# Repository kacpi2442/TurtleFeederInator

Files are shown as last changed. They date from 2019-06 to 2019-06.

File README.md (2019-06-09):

# TurtleFeederInator

Automatic turtle/fish feeder that you can 3D print yourself.
It uses WeMos D1 mini (ESP8266) as main board and features food run out sensor.

It can be powered either from USB or DC Jack (5V).

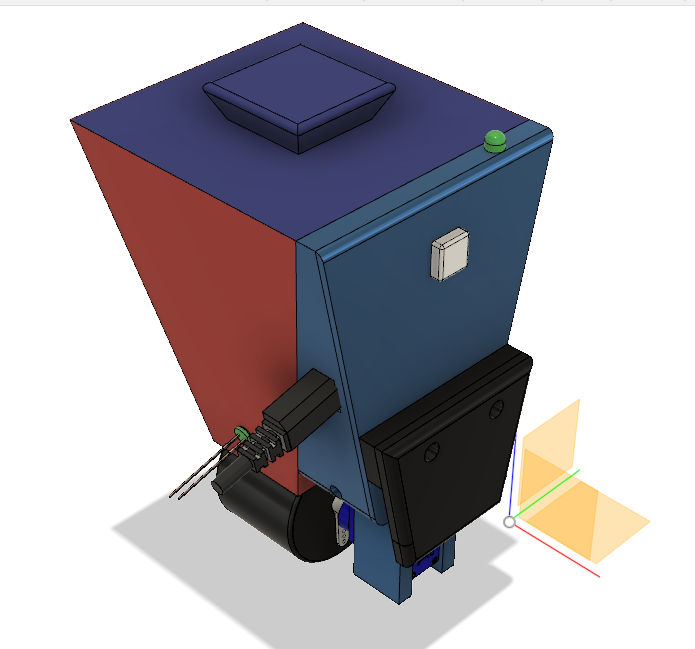
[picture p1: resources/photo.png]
Project view
<br />
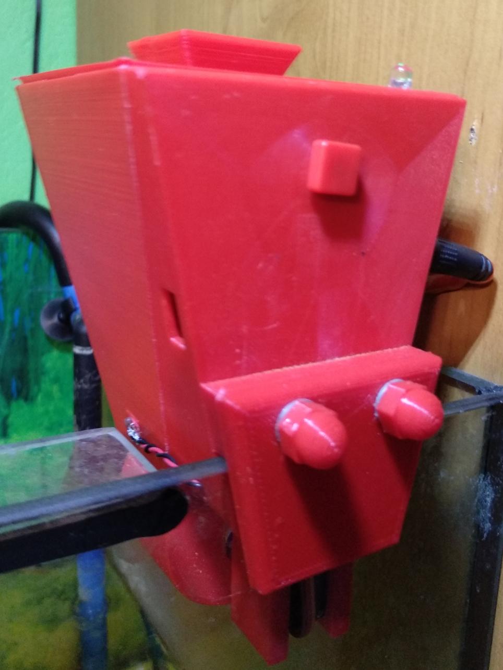
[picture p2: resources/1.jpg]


## Getting Started

### Parts
* WeMos D1 mini (the one with mounting holes)
* SG-90 Servo (or similar)
* 12x12 Tactile push button (TC-1212T) and button cap
* Standard 5.5x2.1mm female DC Jack (i took out one from Arduino UNO)
* 5mm Infrared LED (you can take one from old remote)
* 5mm Infrared photodiode
* 5mm RGB LED with common cathode
* 3x 220Ω Resistor
* 100Ω Resistor
* 2x 20mm M5 hex bolt
* 2x M5 washer (DIN 125)
* 2x M5 hex nut 
* 4x small self-tapping screw (two for mount the servo, and two for mount the D1 mini)
* 2x small silicone washer (they often adding them to computer fans for silencing)
* Some wires (ex. from UTP cable)

### Tools needed
* Soldering iron
* Hot glue gun
* Sandpaper
* Cyanoacrylate glue (ex. Super Glue)

### 3D print

Scale `spacer.stl` to the thickness of your aquarium wall (by default it's 5mm thick).
All the parts you can print with standard PLA. 
#### Recommended settings
| Part | Infill | Supports  |
| --- |:---:| ---:|
| `case.stl` | 30% | no |
| `feeder.stl`  | 25% | yes |
| `hook.stl` | 25% | no |
| `lid.stl` | 25% | optional  |
| `spacer.stl`  | 25% | no |
| `funnel.stl`  | 100% | yes, see bellow|

<br />
When slicing `funnel.stl` you must block generating supports near IR led and photodiode holes, like on the screenshot below.<br />

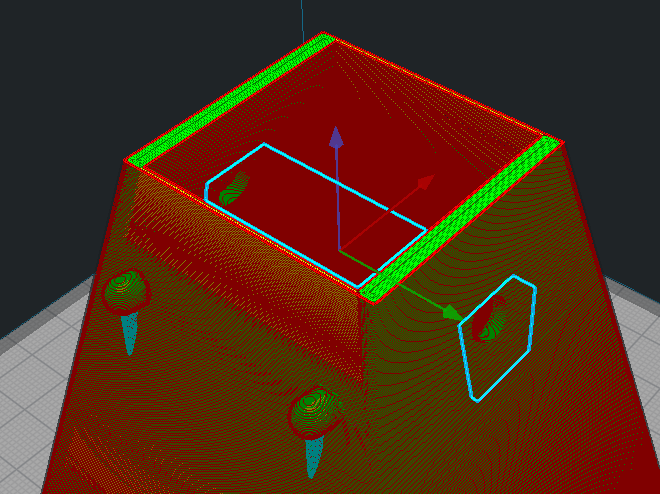
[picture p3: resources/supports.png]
Cura screenshot
<br />
To save some time and material, I suggest unticking "Use towers" in support settings when using Cura.

### Assembly

* Print all the parts
* Solder wires to the IR LED and photodiode, about 8-10cm each
* Solder 220Ω resistor to each anode of the RGB diode (longest leg is a cathode)
* Attach the servo to the `case.stl` using silicone washers and two small plastic screws, put the cable inside the case using a hole on the bottom
* Place M5 hex nuts, push button, DC Jack and RGB LED inside desired holes for them
* Secure the button using hot glue
* Put the IR LED and photodiode cables through the side holes of the case.
* Do all the wiring according to schematic bellow<br />
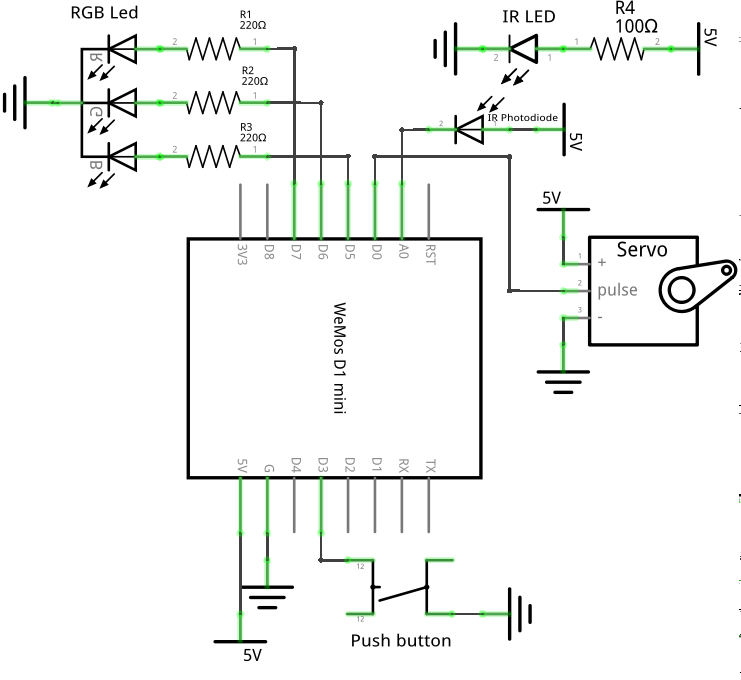
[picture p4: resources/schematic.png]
Schematic

* Secure RGB LED and DC Jack using hot glue
* Secure WeMos using self-tapping screws
* Attach `spacer.stl` and `hook.stl` to `case.stl` using bolts and washers.
* Check if `funnel.stl` fits the `case.stl`, if not use sandpaper on the joints
* Secure `feeder.stl` to the servo using cyanoacrylate glue
* At this point, everything should look like this<br />
This
<sub><sup>Yeah, I know it looks quite messy</sup></sub>
* Attach carefully `funnel.stl`
* Place the IR LED and photodiode inside their holes (they should hold inside them without any glue)
* Upload firmware using USB cable and load it with turtle/fish food

### Firmware
You can use [this firmware](https://github.com/kacpi2442/TurtleFeederFirmware) or write your own.

Create an issue if you want me to add a link to your firmware here.

## Gallery
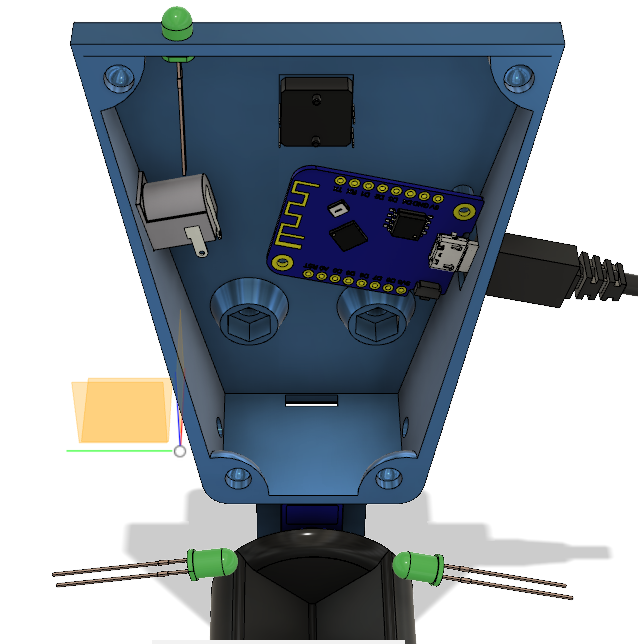
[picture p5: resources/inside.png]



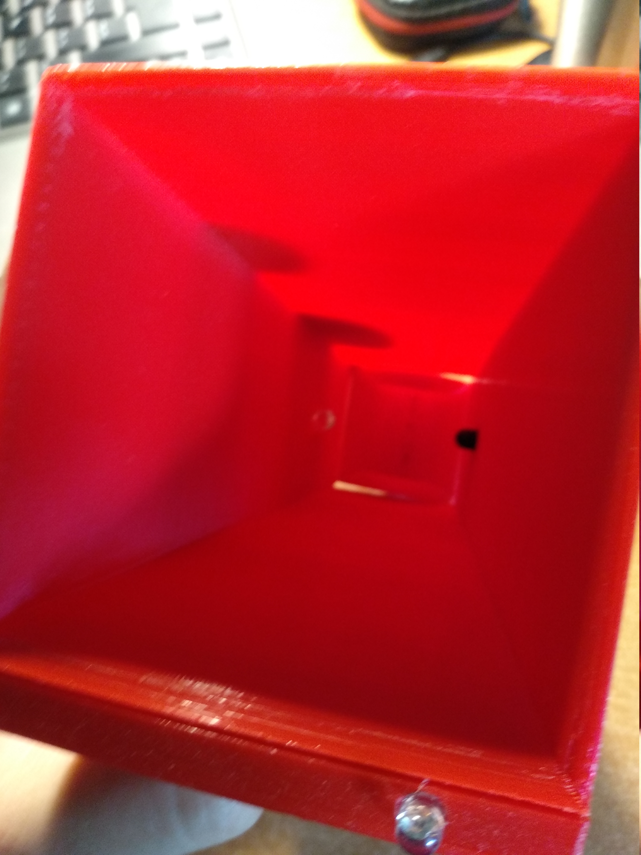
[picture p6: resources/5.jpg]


## Licence
These files are distributed under the terms of [The MIT License (MIT)](LICENSE)

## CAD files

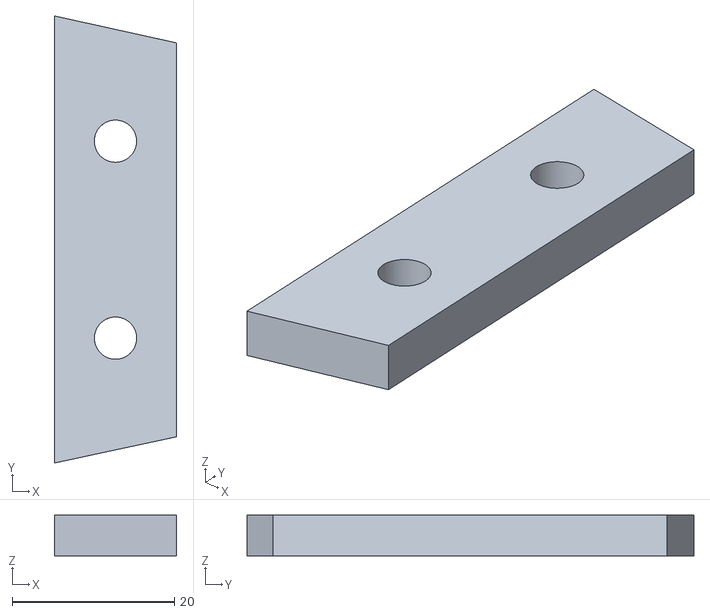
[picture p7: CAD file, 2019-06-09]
STL/spacer.stl
15.0 x 55.1 x 5.01

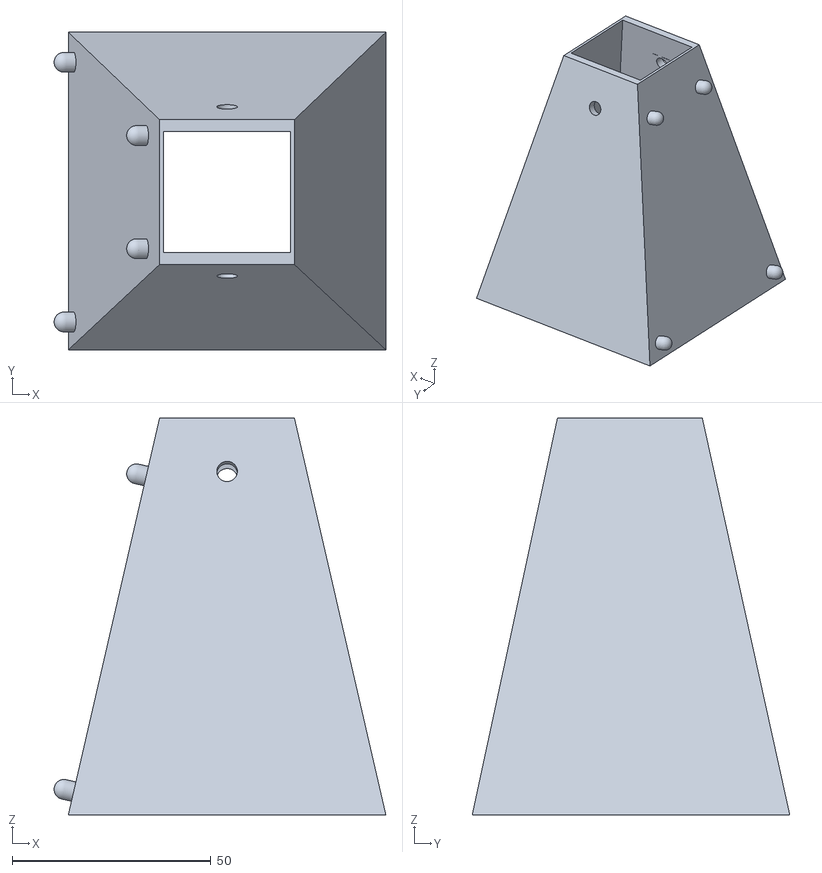
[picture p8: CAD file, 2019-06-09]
STL/funnel.stl
83.6 x 80.0 x 100.0

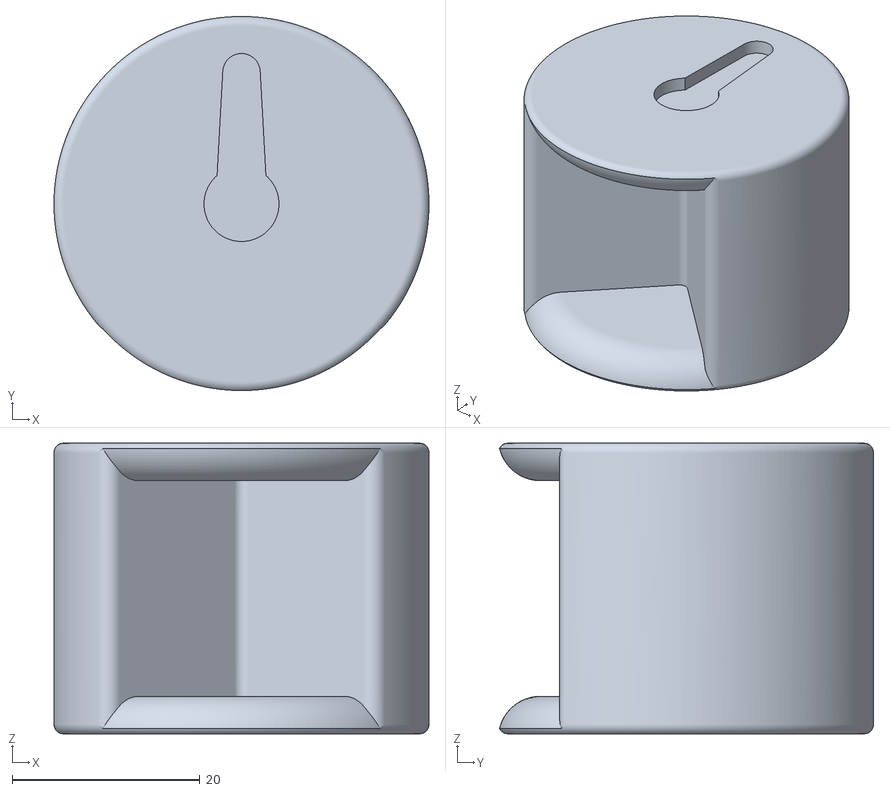
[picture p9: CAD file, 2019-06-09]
STL/feeder.stl
40.0 x 39.9 x 31.0

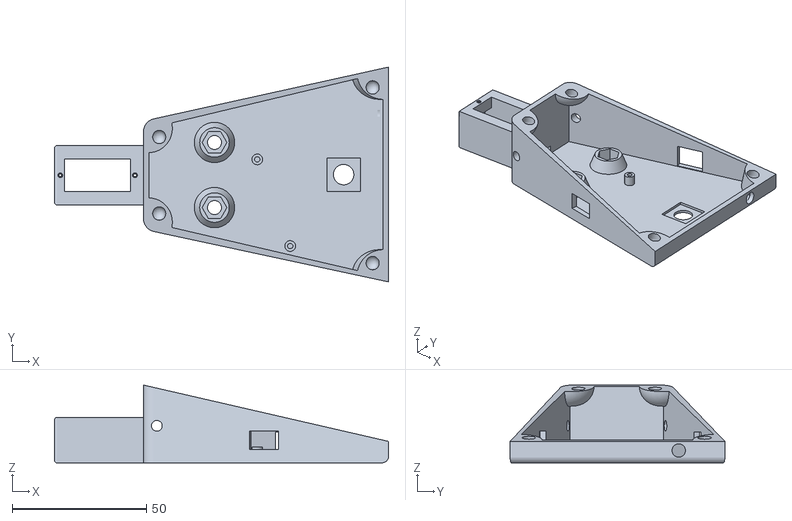
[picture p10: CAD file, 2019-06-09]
STL/case.stl
124.4 x 80.0 x 29.0

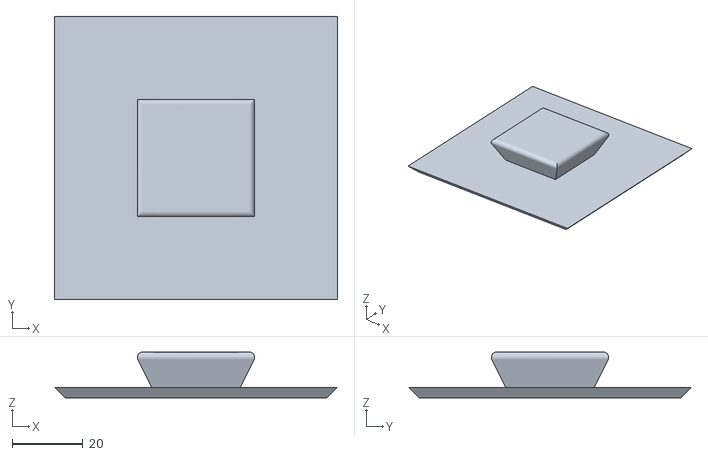
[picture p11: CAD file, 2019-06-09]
STL/lid.stl
80.0 x 80.0 x 13.0

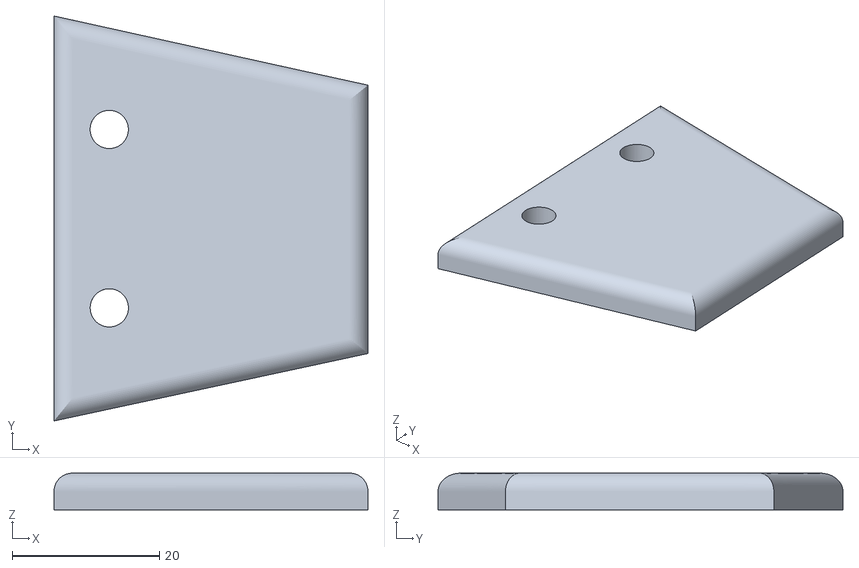
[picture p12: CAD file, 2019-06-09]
STL/hook.stl
42.7 x 55.1 x 5.01
